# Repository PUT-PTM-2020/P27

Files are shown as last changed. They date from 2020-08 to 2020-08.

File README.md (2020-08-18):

# Automat do napojów

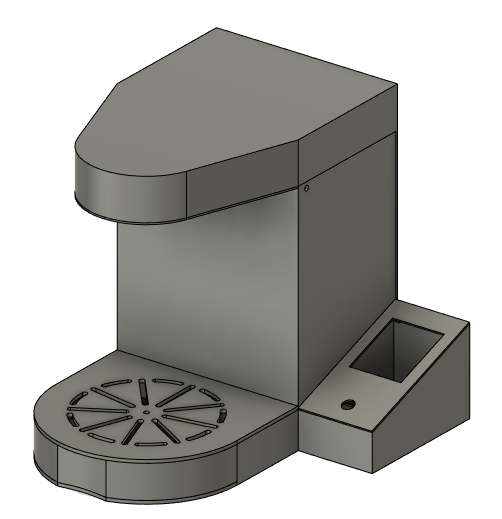
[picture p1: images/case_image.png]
Case image


## Funkcjonalność

- Pomiar wysokości kubka na podstawie wykrywania odległości do dna kubka oraz jego krawędzi
- Nalewanie cieczy z uwzględnieniem maksymalnej bezpiecznej wysokości nalanej cieczy
- Sterowanie menu LCD poprzez enkoder z przyciskiem
- Wybór proporocji dwóch nalewanych cieczy
- Manualne sterowanie silnikami pomp
- Manualne sterowanie serwomechanizmem z zamontowanym czujnikiem odległości
- Odczyt odległości z czujnika

## Wykorzystane elementy

- Płytka STM32F407G-DISC1
- Zasilacz 12V/3A
- 2 przetwornice step-down, 12V -> 3V oraz 12V -> 5V
- Czujnik odległości VL53l0X
- Serwomechanizm SG90s
- Dwukanałowy sterownik silników L293D
- 2 pompy membranowe R385
- Wyświetlacz LCD TFT 1,8'' - Waveshare 13892
- Enkoder z przyciskiem - Waveshare 9533

## Wykorzystane piny

### Enkoder

| Moduł | Układ | Wykorzystanie |
| --- | --- | ----- |
| SIA | PE9 | obrót enkodera (TIM1 Encoder mode CH1+CH2) |
| SIB | PE11 | obrót enkodera (TIM1 Encoder mode CH1+CH2) |
| SW | PB12 | Przycisk enkodera (EXTI12, pull-up, falling edge trigger detection) |
| GND | GND | Masa |
| VCC | 3V | Zasilanie |

### Ekran LCD

| Moduł | Układ | Wykorzystanie |
| --- | --- | ----- |
| VCC | 3V | Zasilanie |
| GND | GND | Masa |
| DIN | PA7 | Linia danych (SPI1) |
| CLK | PA5 | Linia zegarowa (SPI1) |
| CS | PD7 | Chip select, (GPIO output) |
| DC | PC4 | Wybór danych, (GPIO output) |
| RST | PA9 | Reset układu, (GPIO output) |
| BL | - | Podświetlenie - nieużywane |

### Czujnik odległości

| Moduł | Układ | Wykorzystanie |
| --- | --- | ----- |
| VCC | 3V | Zasilanie |
| GND | GND | Masa |
| SCL | PB6 | linia zegara (I2C1, pull-up) |
| SDA | PB7 | linia danych (I2C1, pull-up) |
| GPIO1 | PC1 | Obsługa przerwania EXTI1 oznaczającego nadchodzący wynik pomiaru (pull-up) |
| XSHUT | - | Aktywacja czujnika - nieużywane |

### Serwomechanizm

| Moduł | Układ | Wykorzystanie |
| --- | --- | ----- |
| PWM | PE5 | PWM (TIM9 CH1) |
| VCC | 5V | Zasilanie |
| GND | GND | Masa |

### L293D

| Moduł | Układ | Wykorzystanie |
| --- | --- | ----- |
| ENABLE1 | PB14 | Sterowanie działaniem silnika 1 (GPIO output, pull-down) |
| INPUT1 | 5V | Kierunek silnika 1 |
| OUTPUT1 | Pompa | Zasilanie pompy |
| GND | GND | Masa |
| GND | GND | Masa |
| OUTPUT2 | Pompa | Masa pompy |
| INPUT2 | GND | Kierunek silnika 1 |
| Vs | 12V | Zasilanie układu |
| ENABLE2 | PB15 | Sterowanie działaniem silnika 2 (GPIO output, pull-down) |
| INPUT3 | 5V | Kierunek silnika 2 |
| OUTPUT3 | Pompa | Zasilanie pompy |
| GND | GND | Masa |
| GND | GND | Masa |
| OUTPUT4 | Pompa | Masa pompy |
| INPUT4 | GND | Kierunek silnika 2 |
| Vss | 5V | Zasilanie logiki |

## Timery

- TIM1 - obsługa enkodera w trybie Encoder Mode (CH1 + CH2)
- TIM3 - obsługa procedury mierzenia oraz nalewania cieczy podczas przerwania
- TIM7 - debouncing przycisku enkodera
- TIM9 - PWM serwomechanizmu (CH1)

## Części 3D

Wszystkie części zostały zaprojektowane w Fusion 360 i wydrukowane na drukarce 3D.

Większość wymiarów jest sparametryzowana i można dowolnie zmieniać rozmiar elementów obudowy, ramienia montowanego na serwomechanizmie oraz rurek łączących rurki silikonowe.

## Autorzy

- Tymon Jakubowski - @tjakubowski
- Kamil Mosek - @kamilmosek
- Mateusz Olejnik - @molejnik1998

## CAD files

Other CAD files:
parts/case.f3d
parts/pipes_connector.f3d
parts/sensor_servo_mounting.f3d

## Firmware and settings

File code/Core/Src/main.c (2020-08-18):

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
/* Includes ------------------------------------------------------------------*/
#include "main.h"
#include "i2c.h"
#include "spi.h"
#include "tim.h"
#include "gpio.h"

/* USER CODE BEGIN Includes */
#include <string.h>

// Servo
#include "Servo.h"

// LED screen
#include "lcd_menu.h"

// Pumps
#include "pumps.h"

// Distance sensor
#include "vl53l0x_api.h"

/* USER CODE END Includes */


/* USER CODE BEGIN PV */
// Distance sensor
VL53L0X_RangingMeasurementData_t RangingData;
VL53L0X_Dev_t vl53l0x_c;
VL53L0X_DEV Dev = &vl53l0x_c;

/* USER CODE END PV */

void SystemClock_Config(void);
/**
  * @brief  The application entry point.
  * @retval int
  */
int main(void)
{
  /* USER CODE BEGIN 1 */
  uint32_t refSpadCount;
  uint8_t isApertureSpads;
  uint8_t VhvSettings;
  uint8_t PhaseCal;
  /* USER CODE END 1 */

  /* MCU Configuration--------------------------------------------------------*/

  /* Reset of all peripherals, Initializes the Flash interface and the Systick. */
  HAL_Init();

  /* Configure the system clock */
  SystemClock_Config();

  /* Initialize all configured peripherals */
  MX_GPIO_Init();
  MX_SPI1_Init();
  MX_I2C1_Init();
  MX_TIM1_Init();
  MX_TIM7_Init();
  MX_TIM3_Init();
  MX_TIM9_Init();
  /* USER CODE BEGIN 2 */

  // Init settings variables
  liquid1 = 50;
  liquid2 = 50;

  // Start servo's PWM
  HAL_TIM_PWM_Start(&htim9, TIM_CHANNEL_1);
  servo_set_angle(0, 0);

  // Start encoder channels
  HAL_TIM_Encoder_Start(&htim1, TIM_CHANNEL_ALL);

  // Init of LCD and menu
  menu_init(8, 12);

  // Start pumps
  pumps_init();

  // Init VL53L0X
  Dev->I2cHandle = &hi2c1;
  Dev->I2cDevAddr = 0x52;
  HAL_NVIC_DisableIRQ(EXTI1_IRQn);
  VL53L0X_WaitDeviceBooted( Dev );
  VL53L0X_DataInit( Dev );
  VL53L0X_StaticInit( Dev );
  VL53L0X_PerformRefCalibration(Dev, &VhvSettings, &PhaseCal);
  VL53L0X_PerformRefSpadManagement(Dev, &refSpadCount, &isApertureSpads);
  VL53L0X_SetDeviceMode(Dev, VL53L0X_DEVICEMODE_CONTINUOUS_TIMED_RANGING);
  VL53L0X_SetInterMeasurementPeriodMilliSeconds(Dev, 200);
  VL53L0X_SetGpioConfig(Dev, TOF_EXTI_Pin, VL53L0X_DEVICEMODE_CONTINUOUS_TIMED_RANGING, VL53L0X_GPIOFUNCTIONALITY_THRESHOLD_CROSSED_LOW, VL53L0X_INTERRUPTPOLARITY_LOW);
  VL53L0X_StartMeasurement(Dev);
  HAL_NVIC_EnableIRQ(EXTI1_IRQn);



  /* USER CODE END 2 */

  /* Infinite loop */
  /* USER CODE BEGIN WHILE */
  while (1)
  {
    menu_update();

    /* USER CODE END WHILE */

    /* USER CODE BEGIN 3 */
  }
  /* USER CODE END 3 */
}

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
/* USER CODE BEGIN 4 */
void HAL_GPIO_EXTI_Callback(uint16_t GPIO_Pin)
{
  // Handle distance sensor interrupts
  if(GPIO_Pin == TOF_EXTI_Pin) {
    VL53L0X_GetRangingMeasurementData(Dev, &RangingData);
    VL53L0X_ClearInterruptMask(Dev, VL53L0X_REG_SYSTEM_INTERRUPT_GPIO_NEW_SAMPLE_READY);
    distance_milimeters = RangingData.RangeMilliMeter;
  }

  // Handle encoder interrupts - debounce pressed encoder
  else if(GPIO_Pin == ENCDR_SW_Pin) {
    if(encoder_is_pressed == 0) {
      encoder_is_pressed = 1;
      HAL_TIM_Base_Start_IT(&htim7);
    }
  }

}

void HAL_TIM_PeriodElapsedCallback(TIM_HandleTypeDef *htim)
{
  // Handle pressed, debounced encoder
  if(htim->Instance == TIM7) {
    if(HAL_GPIO_ReadPin(ENCDR_SW_GPIO_Port, ENCDR_SW_Pin) == GPIO_PIN_RESET) {
      encoder_handle_click();
      encoder_is_pressed = 0;
      HAL_TIM_Base_Stop_IT(&htim7);
    }
  }
  // Measurement & pouring timer
  else if(htim->Instance == TIM3) {
    if(menu_state == MENU_STATE_MEASUREMENT)
      perform_cup_height_measurement();
    else if(menu_state == MENU_STATE_POURING)
      perform_pouring();
  }
}

/* USER CODE END 4 */
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


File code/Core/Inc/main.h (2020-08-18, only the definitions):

#define SERVO_PWM_Pin GPIO_PIN_5
#define SERVO_PWM_GPIO_Port GPIOE
#define TOF_EXTI_Pin GPIO_PIN_1
#define TOF_EXTI_GPIO_Port GPIOC
#define TOF_EXTI_EXTI_IRQn EXTI1_IRQn
#define SPI1_SCK_Pin GPIO_PIN_5
#define SPI1_SCK_GPIO_Port GPIOA
#define SPI1_MOSI_Pin GPIO_PIN_7
#define SPI1_MOSI_GPIO_Port GPIOA
#define LCD_DC_Pin GPIO_PIN_4
#define LCD_DC_GPIO_Port GPIOC
#define ENCDR_SIA_Pin GPIO_PIN_9
#define ENCDR_SIA_GPIO_Port GPIOE
#define ENCDR_SIB_Pin GPIO_PIN_11
#define ENCDR_SIB_GPIO_Port GPIOE
#define ENCDR_SW_Pin GPIO_PIN_12
#define ENCDR_SW_GPIO_Port GPIOB
#define ENCDR_SW_EXTI_IRQn EXTI15_10_IRQn
#define PWM1_Pin GPIO_PIN_14
#define PWM1_GPIO_Port GPIOB
#define PWM2_Pin GPIO_PIN_15
#define PWM2_GPIO_Port GPIOB
#define LCD_RST_Pin GPIO_PIN_9
#define LCD_RST_GPIO_Port GPIOA
#define LCD_CS_Pin GPIO_PIN_7
#define LCD_CS_GPIO_Port GPIOD
#define SPI1_MISO_Pin GPIO_PIN_6
#define SPI1_MISO_GPIO_Port GPIOA

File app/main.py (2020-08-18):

from PyQt5.QtWidgets import QApplication, QWidget, QLabel, QGridLayout
from PyQt5.QtWidgets import QLineEdit, QPushButton, QHBoxLayout, QMessageBox
from PyQt5.QtGui import QIcon
from PyQt5.QtCore import Qt
from PyQt5 import QtCore, QtGui, QtWidgets
import sys
import logIn

if __name__ == '__main__':
    app=QApplication(sys.argv)
    window = logIn.LogIn()
    sys.exit(app.exec_())

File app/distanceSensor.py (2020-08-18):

from PyQt5.QtWidgets import QApplication, QWidget, QLabel, QGridLayout
from PyQt5.QtWidgets import QLineEdit, QPushButton, QHBoxLayout, QMessageBox
from PyQt5.QtGui import QIcon
from PyQt5.QtCore import Qt
from PyQt5 import QtCore, QtGui, QtWidgets
import sys
import servomechanism
import membranePump
import send
import menu

global data0
global data1
global data2
global data3


class DistanceSensor(QWidget):
    def __init__(self, parent=None):
        super().__init__(parent)

        pom = send.Send()
        self.send(pom.send('a'))
        self.interfejs()

    def interfejs(self):
        label1 = QLabel("              Hello in Drink Master Servis!", self)
        font = QtGui.QFont()
        font.setPointSize(16)
        label1.setFont(font)


        distanceSensor = QPushButton("&DISTANCE SENSOR",self)
        servomechanism = QPushButton("&SERVOMECHANISM", self)
        membranePumps = QPushButton("&MEMBRANE PUMPS", self)

        distanceSensor.clicked.connect(self.showDistanceSensor)
        servomechanism.clicked.connect(self.showServomechanism)
        membranePumps.clicked.connect(self.showMembranePumps)

        font = QtGui.QFont()
        font.setPointSize(12)

        distanceSensor.setFont(font)
        servomechanism.setFont(font)
        membranePumps.setFont(font)

        label2 = QLabel("Distance Sensor:")
        font = QtGui.QFont()
        font.setPointSize(14)
        label2.setFont(font)

        if data0 != "E":
            label3 = QLabel("ON")
            label4 = QLabel(data2 + "[MM]")
        else:
            label3 = QLabel("OFF")
            label4 = QLabel(" ")




        font = QtGui.QFont()
        font.setPointSize(11)
        label3.setFont(font)
        label4.setFont(font)

        ukladT = QGridLayout()
        ukladT.addWidget(label1,0, 0,1,3)
        ukladT.addWidget(distanceSensor)
        ukladT.addWidget(servomechanism)
        ukladT.addWidget(membranePumps)
        ukladT.addWidget(label2,3,0,1,1)
        ukladT.addWidget(label3,4,0,1,1)
        ukladT.addWidget(label4,4,1,1,1)

        self.setLayout(ukladT)
        self.setGeometry(50, 50, 300, 100)
        # self.setWindowIcon(QIcon("photo.png")) #ikonka trzeba dodać
        self.setWindowTitle("Drink Master Servis")
        self.show()

    def showDistanceSensor(self):
        print("Open Window DistanceSensor")

        self.ds = DistanceSensor()
        self.ds.show()
        self.close()

    def showServomechanism(self):
        print("Open Window Servomechanism")
        self.s = servomechanism.Servomechanism()
        self.s.show()
        self.close()

    def showMembranePumps(self):
        print("Open Window MembranePumps")
        self.mp = membranePump.MembranePump()
        self.mp.show()
        self.close()

    def send(self, i):
        global data0
        global data1
        global data2
        global data3
        data0 = i
        if data0:
            if data0[1] == ';':
                data1 = data0[0]
                if data1 == '0':
                    data2 = data0[2]
                    data2 += data0[3]
                    data2 += data0[4]
                    data2 += data0[5]

                    data3 = data0[7]
                    data3 += data0[8]
                    data3 += data0[9]
                    data3 += data0[10]

                elif data1 == '1':
                    data2 = data0[2]
                    data2 += data0[3]
                    data2 += data0[4]
                    data2 += data0[5]
                    data3 = "0"
                elif data1 == '2':
                    data2 = data0[2]
                    data2 += data0[3]
                    data2 += data0[4]
                    data2 += data0[5]
                    data3 = "0"
            else:
                data2 = data0[0]
                data2 += data0[1]
                data2 += data0[2]
                data2 += data0[3]
                data3 = "0"

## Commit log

2020-05-12 Fix reading TOF sensor value
    [main.c, main.h, ptm-machine.ioc]
2020-05-16 Add TIM4 timer with PWM CH1 generation for handling single motor in L293D
2020-05-16 Fix indentation in main.c
    [main.c]
2020-05-17 encoder init
2020-05-17 add pwm()
2020-05-18 Revert "encoder init"
    This reverts commit 135065937c13fe8745d61b9ff1c4e67d0c3ccbba.
    [main.c, main.h, ptm-machine.ioc]
2020-05-21 encoder button init
2020-05-22 move encoder function from main.cpp to Menu.ccp
2020-05-24 formating code and delete encoder() form main.c
2020-05-26 Change TIM4 settings Add CH2 in TIM4 timer Rename CH1 label to L293D_PWM_1
2020-05-26 Add small library for controlling servo
2020-05-26 Add CH1 PWM in TIM13 timer for servo
2020-05-26 Add basic servo code to set its position from 0 to 90 degrees
2020-05-26 Rename function Servo_set_angle to servo_set_angle
2020-05-28 Replace 4 channel TIM4 with 2 channel TIM12 for L293D
    [main.c, main.h, ptm-machine.ioc]
2020-06-05 Fix handling TOF sensor interrupts and servo rotation
    [main.c, main.h, ptm-machine.ioc]
2020-06-06 Change encoder timer settings
2020-06-06 Add enabling pumps in debug menu
2020-07-27 Add debouncing encoder button
2020-07-27 Change servo pwm pin label
2020-08-16 Refreshed app
    Removal of a minor bug.
    [distanceSensor.py, membranePump.py, servomechanism.py]
2020-08-17 Fix distance sensor errors, servo jittering, screen flickering, random infinite loops, delete redundant outputs, add new menus
    [lcd_menu.c, main.c, main.h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]
2020-08-18 Replace motors PWM with standard output pin, fix menu switching
    [lcd_menu.c, main.c, main.h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]
2020-08-18 Add Fusion 360 parts
    [case.f3d, pipes_connector.f3d, sensor_servo_mounting.f3d]

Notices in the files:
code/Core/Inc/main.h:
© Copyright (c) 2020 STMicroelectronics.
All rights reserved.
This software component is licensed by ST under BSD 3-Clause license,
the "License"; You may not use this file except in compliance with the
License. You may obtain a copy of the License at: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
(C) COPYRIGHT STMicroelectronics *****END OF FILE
